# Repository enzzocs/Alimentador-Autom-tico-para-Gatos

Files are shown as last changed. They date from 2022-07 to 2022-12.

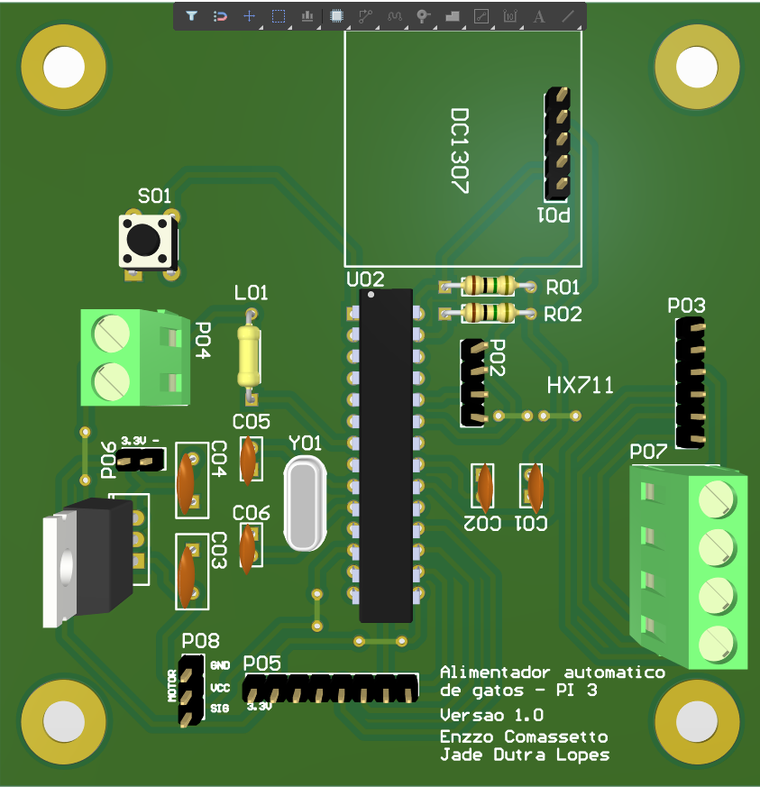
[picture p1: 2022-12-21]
Placa/3D_Superior.png

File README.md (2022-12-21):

# Alimentador Automático de Gatos
Este repositório tem como objetivo relatar as técnicas utilizadas para o desenvolvimentos do projeto de um alimentador automático de gatos. Cada felino é reconhecido por uma tag específica e possui uma porção pré-determinada de ração, baseada na idade e peso do animal. O projeto foi desenvolvido para a displina de Projeto Integrador III, do curso de Engenharia Eletrônica do IFSC Campus Florianópolis, pelos estudantes Enzzo Comassetto dos Santos e Jade Dutra Lopes.

Como referências para a concepção do projeto, foram utilizadas alguns produtos já existentes no mercado, observados nos links a seguir:

[Link 1](https://www.amazon.com.br/PETODAY-Alimentador-Autom%C3%A1tico-Inteligente-Dispensador/dp/B08THNQ36R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)

[Link 2](https://www.amazon.com.br/Prote%C3%A7%C3%A3o-Alimentos-Alimentador-Autom%C3%A1tico-C%C3%A2mera/dp/B0BC9765NC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)

[Link 3](https://www.amazon.com.br/Alimentadores-autom%C3%A1ticos-cronometrados-Dispensador-quantitativo/dp/B09TKS6W6D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)

## 1. A estrutura

   Para o alimentador, foi necessário desenvolver duas seções da estrutura: uma para o armazenamento da ração, e outra para suportar o sistema eletrônico. Utilizou-se um cano para a interligação das seções com o pote de ração fixado na estrutura.
   De material, foi utilizado MDF para a construção do protótipo (figura 1) juntamente de um cano PVC tipo T de 50mm (figura 2) utilizado como o dispenser da ração para o pote. O conjunto foi montado conforme a figura 3.

Figura 1 (https://www.imagemhost.com.br/image/rTlkOC)
Figura 2 (https://www.imagemhost.com.br/image/rTlwlL)
Figura 3 (https://www.imagemhost.com.br/image/rTlzaB)

  De acordo com a progressão das atividades, foi preciso fazer algumas alterações físicas na estrutura. O sensor de peso (que será detalhado mais para frente) foi um grande obstáculo para o andamento do projeto. Esse requeriu mudanças no alimentador para que pudesse operar coerentemente. 
  
## 1.1 Hélice

   Para empurrar a ração ao pote, foi feita em uma impressora 3D uma hélice helicoidal, fixada no servo motor. A ração cai sobre ela, e com o auxílio do motor, a quantidade especificada de ração cai sobre o pote. O design do helicóide foi retirado de um [site](https://www.thingiverse.com/thing:27854) com projeto similar, e ajustado para o tamanho do cano PVC usado. A figura 4 mostra as duas hélices que foram impressas, de 13 e 9cm, respectivamente. A de 13cm foi a utilizada no projeto, enquanto a de 9, como foi resultado de uma impressão falha, foi usada como teste para furos para o encaixe do motor.
  
Figura 4 (https://www.imagemhost.com.br/image/rTlaZK)

   Durante o andamento do projeto, a hélice quebrou no encontro do helicóide com a base. Para consertar, foi colocado um parafuso, que passava pela base e ia por dentro do helicóiode, prendendo a estrutura. Porém isto fez com que a hélice não ficasse perpendicular à base, dificultando a rotação do motor, uma vez que dependendo do ângulo entre o cano e a hélice, o atrito gerado era maior. Isto ocasionava um maior esforço do motor. Dessa forma, o encaixe do mesmo com o cano teve que ser feita de maneira mais cuidadosa.

### 1.2 Motor

  A fim de empurrar a ração para o pote, foi utilizado um [servo motor SM-S4306R 360º](https://www.filipeflop.com/produto/servo-motor-sm-s4306r-360-graus-acessorios/), sem ser necessário o uso de redução para tal. Ele é alimentado em 5V, e funciona por PWM.
  
### 
  
## 2. O projeto

  O alimentador automático de gatos identifica o gato que se aproxima do leitor RFID por uma determinada tag, onde cada gato possui uma porção de ração específica por dia. O motor libera ração o suficiente para completar a porção do gato da vez (monitorado pelo sensor de peso abaixo do pote) para aquele momento do dia.
  
 ## 2.1 Microcontolador
 
  O microcontrolador utilizado foi o **Atmega328P**, inicialmente acoplado em um Arduino Uno. A plataforma do Arduino foi muito útil para os testes iniciais dos sensores e do motor, possibilitando calibrações e detecções de possíveis erros de leitura. Ao fim dos testes individuais, todos sensores foram conectados juntos ao microcontrolador para a integração deles no código final.
  
   Após todos os sensores serem testados, o código foi adaptado para linguagem C no software Atmel Studio.

 ## 2.2 Sensores
 
 ### 2.2.1 Sensor RFID
 
  O sensor **RFID-RC522 13,56MHz** foi utilizado para a identificação de cada felino. Foram utilziadas duas tags diferentes, cada qual com um _id_ diferente para cada gato. Quando a tag é identificada, um sinal é enviado ao motor e este gira a espira até completar a porção necessária.
  
  A ideia original seria o sensor ficar numa posição em frente ao alimentador, sendo capaz de captar a tag do gato. Porém, por ser um protótipo, o sensor ficou em posição de difícil acesso à um gato real, sendo apenas utilizado afim de testes do projeto.
  
 ### 2.2.2 Sensor RTC
 
  O módulo **RTC DS1307** tem a função de controlar o tempo do dia para que o gato não coma mais de 1 porção em determinado período.
  
 ### 2.2.3 Sensor de peso
 
  O sensor de peso com certeza foi o mais complexo para se trabalhar de todo o projeto. Inicialmente, trabalhou-se com uma célula de carga de 50kg juntamente de um **amplificador conversor A/D HX711**. Essa célula de carga funciona de acordo com a deformação que o centro dela sofre de um peso. Para o funcionamento correto da célula, é preciso criar uma base para a mesma, de forma que o centro não fique em contato com a superfície. 
  
  Foi impresso em 3D uma base para a célula de peso, seguindo um [modelo](https://www.thingiverse.com/thing:2624188) achado para o mesmo tipo de célula, de acordo com um [tutorial](https://circuitjournal.com/50kg-load-cells-with-HX711#1x50) para esta aplicação. A figura 5 mostra como ficou a base para o nosso sensor.
  
Figura 5 (https://www.imagemhost.com.br/image/rTBF9Y)

   Entretando, apesar de ter a estrutura para a célula, o sensor continuava a apresentar resultados extremamentes imprecisos, e não conseguia fixar em uma faixa específica de valores. Pesquisando mais a fundo, foram encontrados vários exemplos utilizando não apenas 1, mas 4 dessas células para formar uma balança, o que dificultaria mais ainda criar uma estrutura estável para medir poucas gramas. Dado este enorme problema, a equipe optou por comprar uma balança de peso de alimentos, desmontar a mesma e utilizar a célula de carga + a base desta, como mostra a figura 6. A célula em questão é apresentada na figura 7, é de formato diferente da original e suporta até 10kg. 
   
   Foi então calibrado o sensor, utilizando pesos já conhecidos até obtermos um indice de calibração aceitável.

Figura 6 (https://www.imagemhost.com.br/image/rTB4zI)
Figura 7 (https://www.imagemhost.com.br/image/rTBMxS)

   Esta troca de célula e base foi essencial para o andamento do projeto, pois os resultados foram muito mais precisos e a faixa de valores não alterava conforme o tempo.
  
## 2.3 A placa

   Foi feito o esquemático da placa no software Altium, utilizando o Atmega328P como microcontrolador, juntamente dos sensores listados acima. O design de PCB pode ser visto na figura 8 abaixo.

Figura 8.png

A placa tem dimensão de aproximadamente 9,2x8cm, para caber dentro da estrutura do alimentador. O modelo 3D dela é observado na figura 9.

Figura 9

## 2.4 O código

   Como comentado anteriormente, primeiramente os códigos foram testados na IDE do Arduino, afim de realizar testes e calibrações. Após esta etapa, eles foram integrados e refeitos no Atmel Studio. Foram usadas as seguintes bibliotecas:

```
#include <avr/io.h>
#include <avr/interrupt.h>
#include <stdbool.h>
#include <stdio.h>
#include <stdlib.h>
#include <string.h>
#include <util/delay.h>
#include "utils.h"
#include "spi.h"
#include "mfrc522.h"
#include "twi.h"
```

   Para a leitura do RFID estar sempre disponível e reconhecer uma tag cadastrada a qualquer momento, desligou-se as interrupções do motor até o momento que a tag seja lida pelo sensor.

O código inteiro está disponível neste repositório.

## 3. Custos

   Apesar de alguns sensores e materiais obtidos a partir da impressora 3D terem sido cedidos pelo departamento, o projeto deste protótipo de um alimentador automático de gatos gerou alguns custos para a equipe, como é observado na tabela abaixo.

| Material | Custo | 
| :--- | :---: |
| MDF | R$ 80,00 | 
| Servo motor | R$ 120,00 | 
| Balança de alimentos | R$ 40,00 | 
| Total  | R$ 240,00 |

   Outras alternativas de materiais podem ser obtidas para a construção deste projeto.

## 4. Conclusões

   O alimentador de gatos, após tudo ser montado, ficou como mostra as figuras 10 e 11 abaixo.
   
   Figura 10
   
   Figura 11
   
   A figura 11 mostra o alimentador com a hélice já acoplada, e a figura 10 mostra como a placa foi fixada dentro da estrutura.
   
   [![Vídeo do funcionamento do alimentador]](https://youtube.com/shorts/Q7Cq7R1CHkE?feature=share)

   O projeto apresenteu resultados satisfatórios quando em ambiente controlado. Para funcionamento completo, algumas modificações seriam necessárias, como:
   
   - O RFID utilizado deve possuir um alcance maior (como 10 cm) para a melhor detecção dos gatos;
   - Possuir uma hélice mais resistente, para aguentar o peso da ração sobre ela, sem atrapalhar seu funcionamento;
   - Ser adicionado alguma proteção caso o motor trave;
   - Para um produto final, alguns custos poderiam ser reduzidos, como o material utilizado para a estrutura e o motor da hélice.

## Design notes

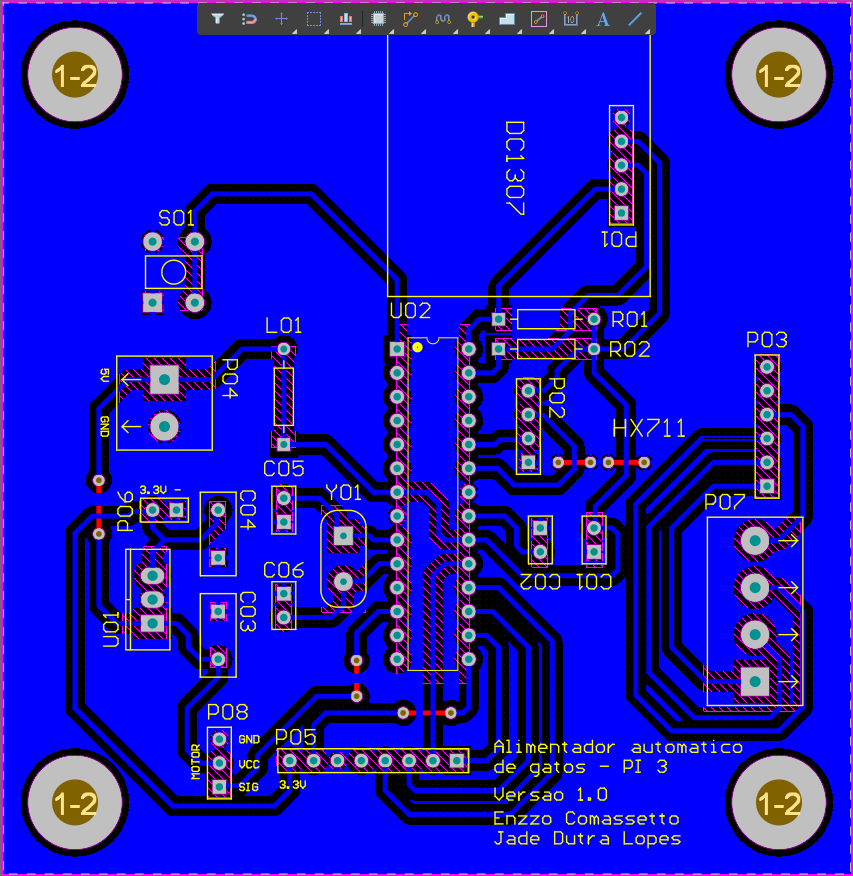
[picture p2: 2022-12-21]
Placa/layout.png

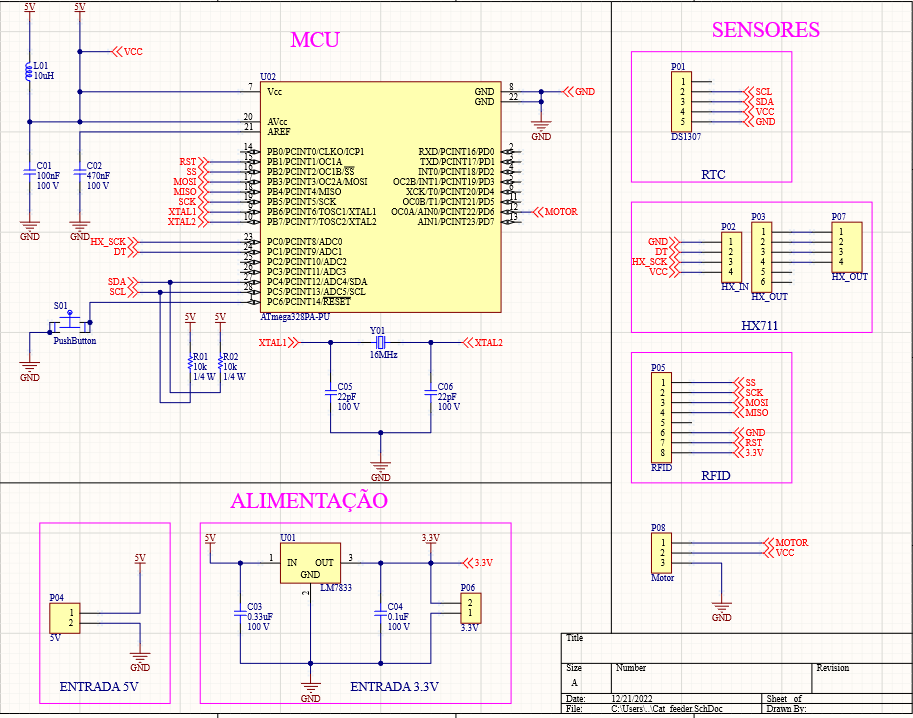
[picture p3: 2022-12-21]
Placa/esquematico.png

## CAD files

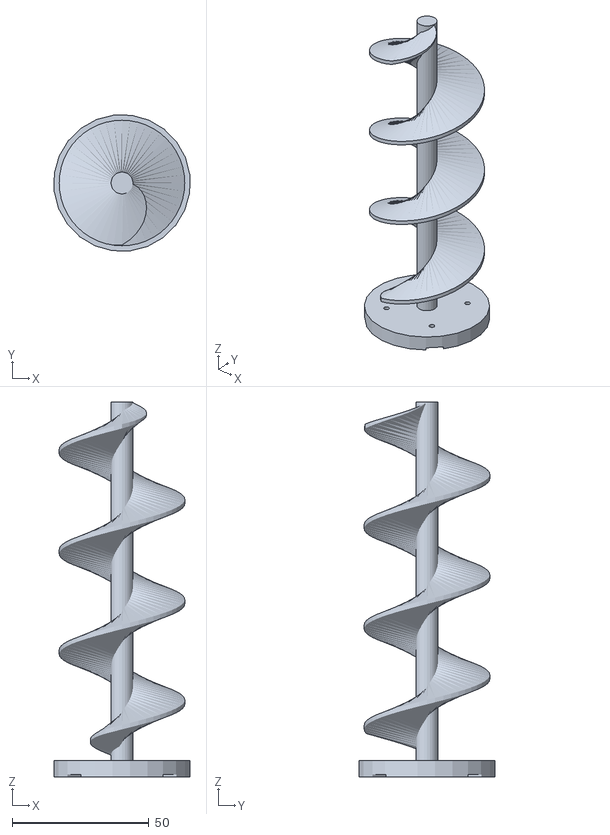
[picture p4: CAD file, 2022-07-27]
Peças 3D/Helicoide.stl
49.6 x 49.6 x 137.0

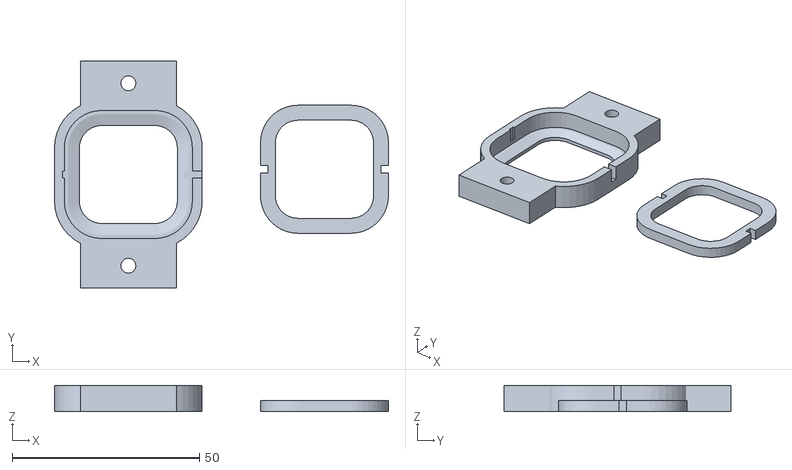
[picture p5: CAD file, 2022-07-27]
Peças 3D/50kgLoadcell-VersionF-2021.stl
89.2 x 60.7 x 7.00

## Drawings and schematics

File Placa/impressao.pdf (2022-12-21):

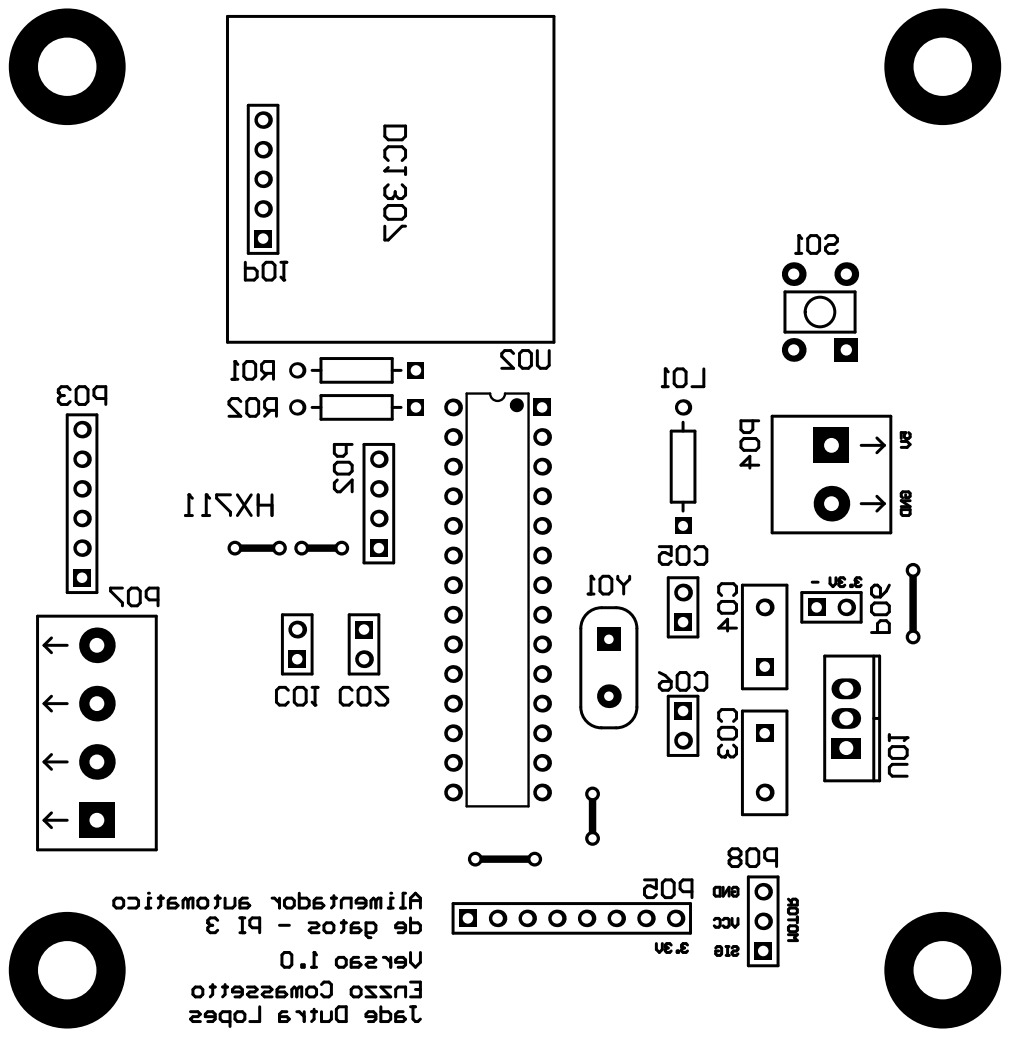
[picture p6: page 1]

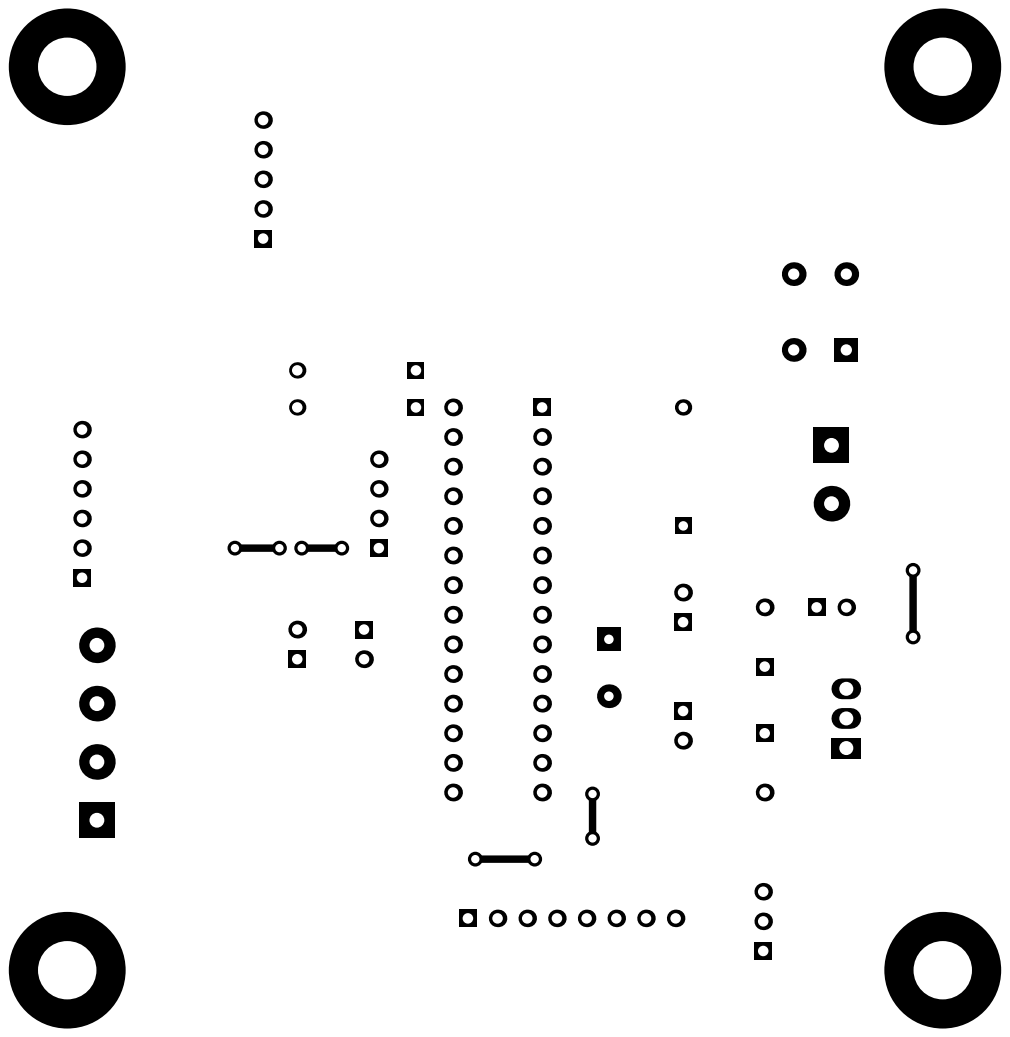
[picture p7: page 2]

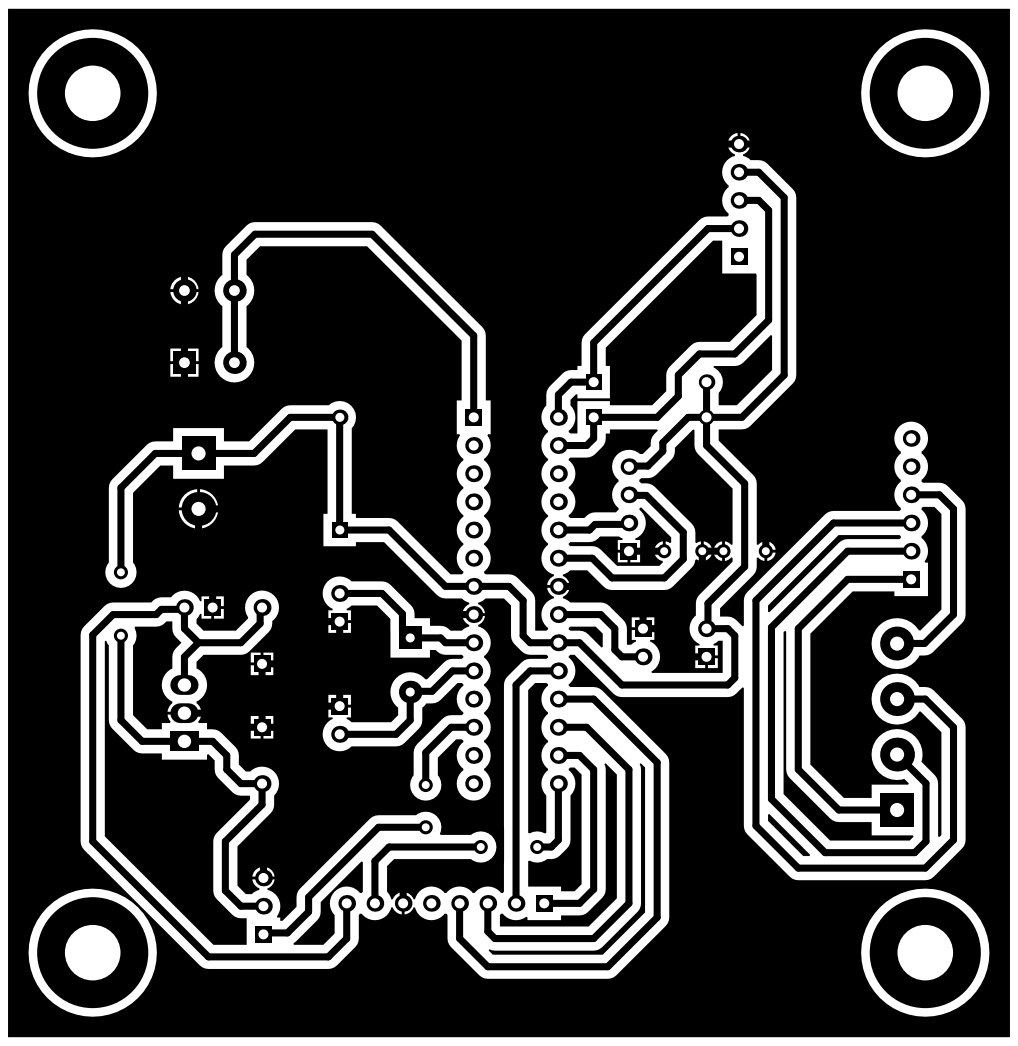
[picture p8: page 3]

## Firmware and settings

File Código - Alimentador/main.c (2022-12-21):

#define F_CPU 16000000UL

#include <avr/io.h>
#include <avr/interrupt.h>
#include <stdbool.h>
#include <stdio.h>
#include <stdlib.h>
#include <string.h>
#include <util/delay.h>
#include "utils.h"
#include "spi.h"
#include "mfrc522.h"
#include "twi.h"

#define BAUD_RATE 9600
#define BAUD_PRESCALE (F_CPU / 16 / BAUD_RATE - 1)

#define set_bit(target, bit) do { (target) |= (1 << (bit)); } while(0)
#define clr_bit(target, bit) do { (target) &= ~(1 << (bit)); } while(0)
#define read_bit(source, bit) ((source) & (1 << (bit)))

#define HX711_DO_DDR DDRC
#define HX711_DO_PORT PORTC
#define HX711_DO_PIN PINC
#define HX711_DO_BIT 1
#define HX711_SK_DDR DDRC
#define HX711_SK_PORT PORTC
#define HX711_SK_BIT 0

void usart_init() {
	UBRR0H = (BAUD_PRESCALE >> 8);
	UBRR0L = BAUD_PRESCALE;
	UCSR0B = (1 << RXEN0) | (1 << TXEN0);
	UCSR0C = (1 << UCSZ01) | (1 << UCSZ00);
}

int usart_send_byte(char byte, FILE *stream) {
	if (byte == '\n') {
		usart_send_byte('\r', stream);
	}
	
	while(!read_bit(UCSR0A, UDRE0));
	
	UDR0 = byte;
	
	return 0;
}

int usart_receive_byte(FILE *stream) {
	while(!read_bit(UCSR0A, RXC0));
	return UDR0;
}

FILE uart_output = FDEV_SETUP_STREAM(usart_send_byte, NULL, _FDEV_SETUP_WRITE);
FILE uart_input = FDEV_SETUP_STREAM(NULL, usart_receive_byte, _FDEV_SETUP_READ);

void hx711_init() {
	// DO = input, no pull up
	clr_bit(HX711_DO_PORT, HX711_DO_BIT);
	clr_bit(HX711_DO_DDR, HX711_DO_BIT);
	
	// SK = output, initial state low
	clr_bit(HX711_SK_PORT, HX711_SK_BIT);
	set_bit(HX711_SK_DDR, HX711_SK_BIT);
}

int32_t hx711_read() {
	uint32_t read_value = 0;
	
	while (read_bit(HX711_DO_PIN, HX711_DO_BIT));
	
	for (uint8_t i = 0; i < 24; i += 1) {
		set_bit(HX711_SK_PORT, HX711_SK_BIT);
		read_value <<= 1;
		clr_bit(HX711_SK_PORT, HX711_SK_BIT);
		if (read_bit(HX711_DO_PIN, HX711_DO_BIT)) {
			read_value |= 1;
		}
	}
	set_bit(HX711_SK_PORT, HX711_SK_BIT);
	read_value ^= 0x800000;
	clr_bit(HX711_SK_PORT, HX711_SK_BIT);

	return ((int32_t)read_value - 8337300) / 368;
}

int32_t hx711_read_average() {
	static uint8_t current = 0;
	int32_t values[10] = {0};
	values[current] = hx711_read();
	current = (current + 1) % 10;
	int32_t sum = 0;
	for (uint8_t i = 0; i < 10; i += 1) {
		sum += values[i];
	}
	return sum / 10;
}

volatile uint8_t refilling = 0;

ISR (TIMER2_COMPA_vect)
{
	if (refilling) {
		OCR0A += 2;
	}
}

uint8_t mfrc522_get_serial(uint8_t* str) {
	uint8_t baiti = mfrc522_request(PICC_REQALL, str);
	
	if(baiti == CARD_FOUND) {
		baiti = mfrc522_get_card_serial(str);
	}
	
	return baiti;
}

uint8_t tags[2][MAX_LEN] = {
	{ 0x35, 0x88, 0xCF, 0x65, 0x17, 0xB5, 0x76, 0xFF, 0x20, 0x7B, 0xEE, 0x6B, 0xD2, 0x2E, 0xEC, 0x3E },
	{ 0xBE, 0xBF, 0x65, 0x03, 0x67, 0xB5, 0x76, 0xFF, 0x20, 0x7B, 0xEE, 0x6B, 0xD2, 0x2E, 0xEC, 0x3E },
};

int32_t refill_quantities[] = { 5, 8 };
uint32_t last_feeding_time[] = { 0, 0 };

uint8_t are_tags_equal(uint8_t* tag1, uint8_t* tag2) {
	for (uint8_t i = 0; i < 5; i += 1) {
		if (tag1[i] != tag2[i]) {
			return 0;
		}
	}
	return 1;
}

typedef struct {
	uint8_t hours;
	uint8_t minutes;
	uint8_t seconds;
} time_t;

time_t get_current_time() {
	uint8_t set_ds1307_addr[1] = {0};
	uint8_t ds1307_received_data[3];

	twi_start_transceiver();
	twi_transmit_data(0x68, set_ds1307_addr, 1);
	twi_request_data(0x68, 3);
	twi_get_received_data(ds1307_received_data, 3);

	uint8_t seconds = 10 * ((ds1307_received_data[0] & 0x70) >> 4) + (ds1307_received_data[0] & 0x0F);
	uint8_t minutes = 10 * ((ds1307_received_data[1] & 0x70) >> 4) + (ds1307_received_data[1] & 0x0F);
	uint8_t is_am_pm_mode = ds1307_received_data[2] & (1 << 6);
	uint8_t hours = ds1307_received_data[2] & 0x0F;
	if (is_am_pm_mode) {
		hours += (ds1307_received_data[2] & 0x10) >> 4;
		uint8_t is_pm = ds1307_received_data[2] & (1 << 5);
		hours += is_pm ? 12 : 0;
		} else {
		hours += (ds1307_received_data[2] & 0x30) >> 4;
	}

	return (time_t){
		.hours = hours,
		.minutes = minutes,
		.seconds = seconds,
	};
}

uint32_t current_time_to_timestamp(time_t current_time) {
	return current_time.hours * 60 * 60 + current_time.minutes * 60 + current_time.seconds;
}

int main() {
	//controla pwm
	DDRD |= _BV(PD6);
	TCCR0A |= _BV(COM0A1) | _BV(WGM00);
	TCCR0B |= _BV(CS00) | _BV(WGM02);
	TCCR0A |= _BV(WGM20);
	//incrementa o pwm
	TCCR2B |= _BV(CS20) | _BV(CS21) | _BV(CS22);
	TIMSK2 |= _BV(OCIE2A);
	OCR2A = 182; 
	
	uint8_t str[MAX_LEN];
	uint8_t baiti = CARD_NOT_FOUND;
	OCR0A = 0; //
	
	spi_init();
	_delay_ms(1000);
	mfrc522_init();
	usart_init();
	hx711_init();
	twi_master_init();
	
	stdout = &uart_output;
	_delay_ms(10);
	//Desabilita interrupção do TIMER 2
	TIMSK2 &= ~_BV(OCIE2A);
	//Habilita Interrupções Globais
	sei();
	
	//Debug
	printf("Starting...\n");
	time_t time = get_current_time();
	time_t feeding_interval = (time_t){ .hours = 0, .minutes = 3, .seconds = 0 };
	uint32_t feeding_interval_timestamp = current_time_to_timestamp(feeding_interval);
	uint32_t timestamp = current_time_to_timestamp(time);
	last_feeding_time[0] = timestamp - feeding_interval_timestamp;
	last_feeding_time[1] = timestamp - feeding_interval_timestamp;

	uint8_t refill_target = 0;

	while (1) {
		baiti = mfrc522_get_serial(str);

		if (baiti != CARD_FOUND) {
			continue;
		}
		//Debug
		printf("Card detected: [");
		for (uint8_t i = 0; i < MAX_LEN; i += 1) {
			printf("%02X", str[i]);
		}
		printf("]\n");

		//Cartão encontrado
		//Verifica Se o cartão esta registrado
		for (uint8_t i = 0; i < 2; i += 1) {
			if (!are_tags_equal(tags[i], str)) {
				printf("%u fail\n", i);
				continue;
			}

			printf("%u success\n", i);

			uint32_t current_timestamp = current_time_to_timestamp(time);
			uint32_t next_feeding_timestamp = last_feeding_time[i] + current_time_to_timestamp(feeding_interval);
			//Compara se o gato ja pode ser alimentado pelo tempo dês de a ultima alimentação
			if (current_timestamp >= next_feeding_timestamp) {
				last_feeding_time[i] = current_timestamp;
				refilling = 1;
				refill_target = i;
				printf("Refilling for %u until %li grams...\n", i, refill_quantities[refill_target]);
				} else {
				printf("A refill is still not available for this cat\n");
			}
			//Liga o giro do motor ate chegar no peso de ração adequado
			TIMSK2 |= _BV(OCIE2A);
			while (1) {
				int32_t weight = hx711_read_average();
				printf("Current weight = %li\n\n", weight);

				if (weight >= refill_quantities[refill_target]) {
					break;
				}
			}
			TIMSK2 &= ~_BV(OCIE2A);
		}
		
	}
}

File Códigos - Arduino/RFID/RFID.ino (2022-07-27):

#include <Wire.h> //INCLUSÃO DA BIBLIOTECA NECESSÁRIA
#include <SPI.h> //INCLUSÃO DE BIBLIOTECA
#include <MFRC522.h> //INCLUSÃO DE BIBLIOTECA

#define SS_PIN 10 //PINO SDA
#define RST_PIN 9 //PINO DE RESET

MFRC522 rfid(SS_PIN, RST_PIN); //PASSAGEM DE PARÂMETROS REFERENTE AOS PINOS


const int pinoLedVerde = 3; //PINO DIGITAL REFERENTE AO LED VERDE
const int pinoLedVermelho = 2; //PINO DIGITAL REFERENTE AO LED VERMELHO
int motor_pwm = 6; // pino do led

void setup(){

  Wire.begin(); //INICIALIZA A BIBLIOTECA WIRE
  SPI.begin(); //INICIALIZA O BARRAMENTO SPI
  rfid.PCD_Init(); //INICIALIZA MFRC522
  
  pinMode(pinoLedVerde, OUTPUT); //DEFINE O PINO COMO SAÍDA
  pinMode(pinoLedVermelho, OUTPUT); //DEFINE O PINO COMO SAÍDA
  pinMode(motor_pwm, OUTPUT); // configura pino como saída
  
  digitalWrite(pinoLedVerde, LOW); //LED INICIA DESLIGADO
  digitalWrite(pinoLedVermelho, LOW); //LED INICIA DESLIGADO
}

void loop() {
  leituraRfid(); //CHAMA A FUNÇÃO RESPONSÁVEL PELA VALIDAÇÃO DA TAG RFID
}

//FUNÇÃO DE VALIDAÇÃO DA TAG RFID
void leituraRfid(){
  if (!rfid.PICC_IsNewCardPresent() || !rfid.PICC_ReadCardSerial()) //VERIFICA SE O CARTÃO PRESENTE NO LEITOR É DIFERENTE DO ÚLTIMO CARTÃO LIDO. CASO NÃO SEJA, FAZ
    return; //RETORNA PARA LER NOVAMENTE

  /***INICIO BLOCO DE CÓDIGO RESPONSÁVEL POR GERAR A TAG RFID LIDA***/
  String strID = ""; 
  for (byte i = 0; i < 4; i++) {
    strID +=
    (rfid.uid.uidByte[i] < 0x10 ? "0" : "") +
    String(rfid.uid.uidByte[i], HEX) +
    (i!=3 ? ":" : "");
  }
  strID.toUpperCase();
/***FIM DO BLOCO DE CÓDIGO RESPONSÁVEL POR GERAR A TAG RFID LIDA***/

  //O ENDEREÇO "27:41:AA:AB" DEVERÁ SER ALTERADO PARA O ENDEREÇO DA SUA TAG RFID QUE CAPTUROU ANTERIORMENTE
  if (strID.indexOf("35:88:CF:65") >= 0) { //SE O ENDEREÇO DA TAG LIDA FOR IGUAL AO ENDEREÇO INFORMADO, FAZ
    digitalWrite(pinoLedVerde, HIGH); //LIGA O LED VERDE
    analogWrite(motor_pwm, 128);
    delay(3000); //INTERVALO DE 4 SEGUNDOS
    analogWrite(motor_pwm, 0);
    digitalWrite(pinoLedVerde, LOW); //DESLIGA O LED VERDE
    
  }else{ //SENÃO, FAZ (CASO A TAG LIDA NÃO SEJÁ VÁLIDA)
    digitalWrite(pinoLedVermelho, HIGH); //LIGA O LED VERMELHO
    analogWrite(motor_pwm, 128);
    delay(3000); ////INTERVALO DE 6 SEGUNDOS
    analogWrite(motor_pwm, 0);
    digitalWrite(pinoLedVermelho, LOW); //DESLIGA O LED VERDE
    
  }

  rfid.PICC_HaltA(); //PARADA DA LEITURA DO CARTÃO
  rfid.PCD_StopCrypto1(); //PARADA DA CRIPTOGRAFIA NO PCD
  }
